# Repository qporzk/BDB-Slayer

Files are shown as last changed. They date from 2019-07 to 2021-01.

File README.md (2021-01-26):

# BDB-Slayer

## NOTE

IF YOU ARE GOING TO PRINT THE STUFF FOR THE JAKE VALVE, SEE NOTE AT BOTTOM OF THIS PAGE

I'm trying out some doc hosting stuff on this repo for fun and to make it look a bit nicer. The readthedocs page is here: https://qporzk.github.io/BDB-Slayer/

This repo is meant to be a knowledge base for mods to the Breville Dual Boiler espresso machine. This focuses on (but is not limited to) the rerouting of tubes to the hot water needle valve to enable flow profiling. Background here: https://www.home-barista.com/espresso-machines/breville-dual-boiler-slayer-shots-t54849.html

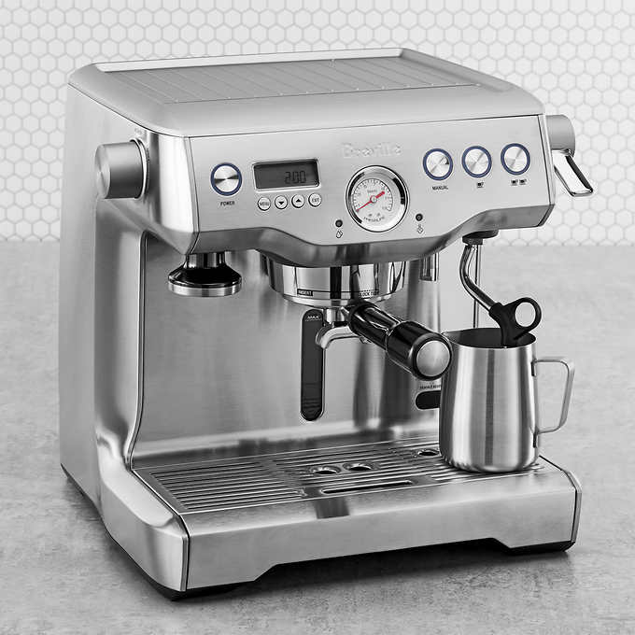
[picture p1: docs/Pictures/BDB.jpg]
Sample Image


## Sections

Slayer Mod
  - This is a pictorial guide to doing this mod

Pulling with the Slayer Mod
  - This focuses on actually pulling shots once the mod is completed. This includes how the pulls work, what the best profiles are, and theory on profiles.

Upgrades
  - This focuses on other upgrades that can be made, including replacing the needle valve, replacing the pump, plumbing in, and others.

Maintenance
  - This covers maintenance, both preventative and reactive, as well as general routine maintenace and cleanup that should be performed

## Models

NOTE: These models are out of date, as they were made for my BDB which was slightly broken. The portion of the body where the hot water knob attaches has a flange that I was unaware of as it was broken off on my machine. I've added an updated .f3d file called "BDB Marker Knob Stock" which may work for new machines, but may need the recess in the knob and cutting of fins on the Drive to be increased in size/depth, as I've only estimated the size of the flange from pictures. If you edit this to fit well on a stock machine, let me know and I can update the model.

This will summarize the 3D models included in the repo, as far as what they are, what they replace, and best practices for acquiring them.

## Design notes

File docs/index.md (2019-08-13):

# BDB-Slayer

## NOTE

I'm trying out some doc hosting stuff on this repo for fun and to make it look a bit nicer. The readthedocs page is here: [GitHub Pages Site](https://qporzk.github.io/BDB-Slayer/)

This repo is meant to be a knowledge base for mods to the Breville Dual Boiler espresso machine. This focuses on (but is not limited to) the rerouting of tubes to the hot water needle valve to enable flow profiling. Background here: [Home Barista Thread](https://www.home-barista.com/espresso-machines/breville-dual-boiler-slayer-shots-t54849.html)

Sample Image

## Sections

Slayer Mod
  - This is a pictorial guide to doing this mod
  
Pulling with the Slayer Mod
  - This focuses on actually pulling shots once the mod is completed. This includes how the pulls work, what the best profiles are, and theory on profiles.
  
Upgrades
  - This focuses on other upgrades that can be made, including replacing the needle valve, replacing the pump, plumbing in, and others.
  
Maintenance
  - This covers maintenance, both preventative and reactive, as well as general routine maintenace and cleanup that should be performed

## Models

[Models for 3D printing can be found here.](https://github.com/qporzk/BDB-Slayer/tree/master/docs/Models)

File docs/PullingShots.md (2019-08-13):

# Pulling Shots
 This will outline different methods to pull shots once the Slayer Mod has been performed.

## Classic Slayer Shot
This mimics the typical shot that would be pulled on an actual Slayer

### Setup
- Set needle valve to barely open 
- Place cup on scale under grouphead
- Hold single cup button to run pump
- Let pump run for 10 seconds
- Divide weight of water by 10 to get your flowrate in ml/s
- Adjust valve and rerun test until you get 1.4ml/s
- Make a mark on the machine so save this position
- Set preinfusion time to 0 seconds

### The Pull
- Install portafilter
- Set valve to 1.4ml/s mark
- Press manual button to start shot
- Preinfuse for desired time
  - Aim to start pressure ramp around 18s
  - First drops should start around 20s 
  - Pressure should get to 9 bar at about 25s
- Open valve for desired amount of full flow time
  - Aim for 2/3 of your total output weight
- Set valve back to 1.4ml/s mark
- Press manual button to stop the shot when target weight is reached (or a bit before)

## Blooming Espresso Shot
This shot mimics the blooming espresso outlined in Scott Rao's blog post: https://www.scottrao.com/blog/2018/7/18/advanced-mode-on-the-de1

### Setup
- Perform pump kill switch mod
- Find and mark 4ml/s point as above
- Find and mark 2.2ml/s point as above
- Set preinfusion time to 0 seconds

### The Pull
- Install portafilter
- Set valve to 4ml/s mark
- Press manual button to start shot
- Preinfuse until pressure ramps to 4bar
- Use kill switch to turn off the pump
- Wait for 30 seconds
- Set valve to 2.2ml/s
- Turn pump back on
- Run shot to desired output weight

## Normal shot
This is just a normal shot ¯\\\_(ツ)_/¯\

### Setup
- Set preinfusion time to desired amount

### The Pull
- Install portafilter
- Set valve wide open
- Press manual button to start shot
- Run shot to desired output weight

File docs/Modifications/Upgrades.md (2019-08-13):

This focuses on other upgrades that can be made, including replacing the needle valve, replacing the pump, plumbing in, and others.

## [Wooden PF Handles](https://www.wilcoxcoffeeparts.com.au/product-category/breville/breville-portafilter-handles/)

## [Brass OPV and Pump Upgrade](https://www.home-barista.com/repairs/breville-dual-boiler-bes900xl-brass-opv-and-pump-mod-t43690.html)

[Alternative Upgrade Site](http://nic.steve-tek.com/?page_id=364)

- [OPV](https://www.espressocare.com/products/item/vibiemme-bypass-valve-opv)
- [Elbow](https://www.ebay.com/itm/1-8-Bsp-Pour-4mm-Compression-Coude-Fixation-Air-Liquide-Qty2-b231-/112089724410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)
- [Pump](https://www.amazon.com/dp/B00B8KBVZE/ref=cm_sw_r_cp_apa_i_7.XmDb7FMQCEF)

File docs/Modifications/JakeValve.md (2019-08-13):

# Summary

This doc covers the "Jake Valve", a replacement for the Hot Water Needle Valve discovered/designed by Jake_G from Home-Barista.

## BOM

- [Clippard Valve](https://www.clippard.com/part/M-MNV-1K)
- [Male push connects](https://www.amazon.com/gp/product/B01N6JF205/ref=ppx_yo_dt_b_asin_image_o00_s00?ie=UTF8&psc=1)
- [Female push connects](https://www.amazon.com/gp/product/B01N6JF205/ref=ppx_yo_dt_b_asin_image_o00_s00?ie=UTF8&psc=1)
- 3D printed shaft and housing

## Procedure

- Remove top cover
- Remove hot water knob by popping off cover and unscrewing screw in center of knob
- Remove two screws holding valve to frame
- Remove two screw holding valve mount inside
- Disconnect two tubes from valve and remove old valve
- Screw female push connect into new valve
- Slide 3D printed shaft onto new valve shaft
- Slide new valve into 3D printed housing, 3D printed shaft first
- Screw male push connect into new valve through hole in housing
- Slide internal mounting bracket onto new assembly
- Reattach tubes
- Reassemble

## Cross section of new assembly

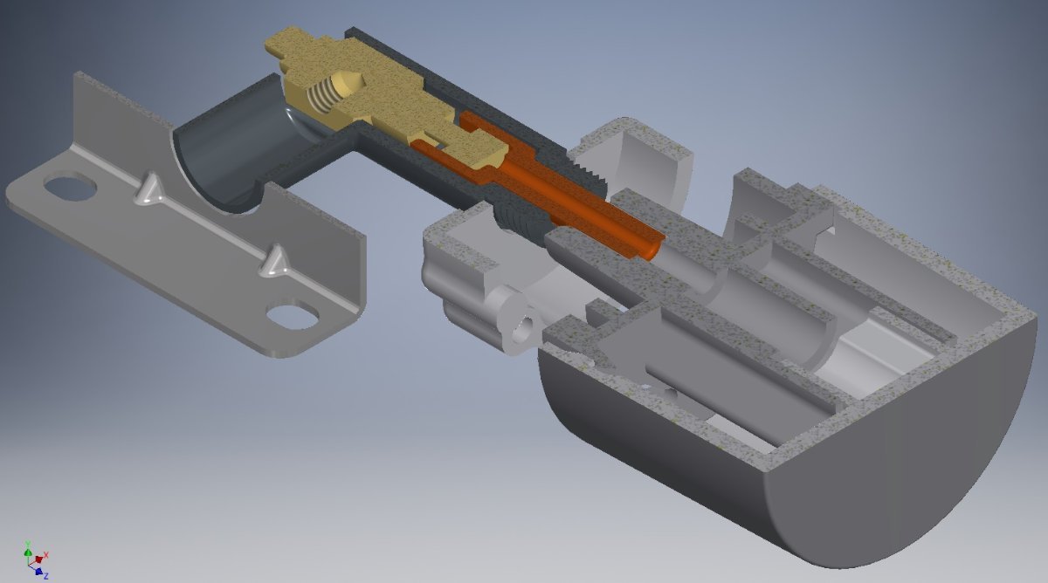
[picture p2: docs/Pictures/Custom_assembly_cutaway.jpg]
Cross Section


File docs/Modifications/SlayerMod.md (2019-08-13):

# BDB Slayer Mod

This outlines the steps needed to perform the Slayer mod on a stock machine as written by user Spitz.me on the Home-Barista forum: https://www.home-barista.com/member/Spitz.me/

## STOCK tube setup on a BDB 920

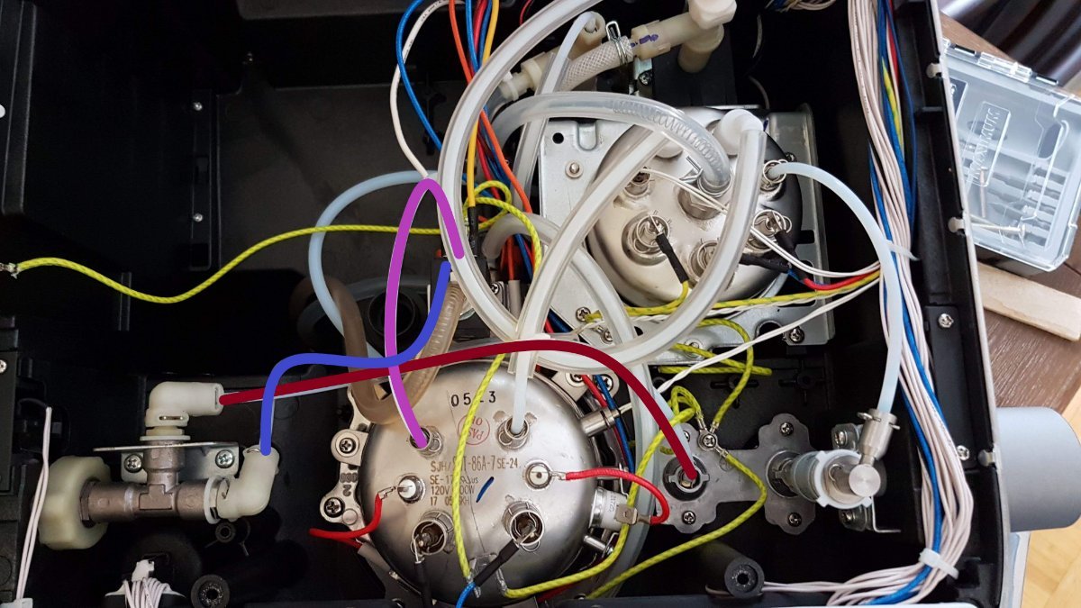
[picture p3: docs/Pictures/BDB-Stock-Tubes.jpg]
Stock BDB tube setup


This is an image taken from the front of the machine so the bottom of the image is the front of the machine.

I'll list the tubes in the order that I did my modification. Also think of the needle valve as a "T". The portion of the needle valve that points to the back of the machine is the middle of the "T". One side of the "T" is the hot water knob.

The tubes have fittings near the ends. These need to go below the hairpin to install the tubes properly. The hairpins can be easily pulled with pliers and they reinstall very easily. This will make more sense when you start working with the tubes.

The tubes may or may not come out with little orange gaskets. You're going to be moving different ends around and even moving an entire tube to a new location. The best thing to do is to take the gaskets with the tubes. If you can't, like I couldn't for one of them, then just be smart about it and move a gasket to another tube. As Ryan pointed out, if you're not careful about your gaskets you could potentially force them awkwardly into the holes and this isn't good.

**Light Purple Tube - Boiler to the solenoid (black box behind the brew boiler)**

**Maroon (dark red) Tube - Needle valve (middle "T" pointing to back) to the hot water tap.**

**Blue Tube - Needle Valve (side "T" pointing to boiler) to the solenoid.**

My tubes and fittings are not the same across all 900s or 920s, I don't believe, but someone smarter can correct me here. I know Peter's 900 has different stock tube fittings. On my machine, all of the tubes I needed to shift had the same hairpin fittings on both ends. I believe my tube hairpin fittings made it easier because removing the tubes from the solenoid would have made it trickier . You can kind of make it out in the picture that the tubes into the solenoid are buried a bit.

## Modified BDB with color coded tubes now in new positions
Detach both tubes from the needle valve. It makes it easier to work through.

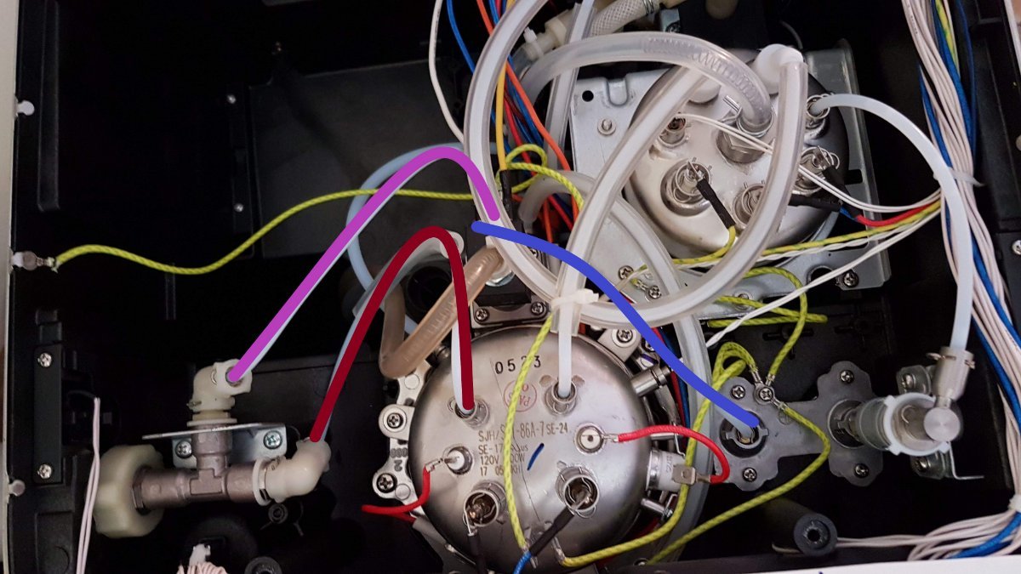
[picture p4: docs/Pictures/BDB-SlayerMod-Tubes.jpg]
Slayer Mod BDB tube setup


### New Configuration:
**Light Purple Tube - Removed from the top of the brew boiler and fitted to the needle valve (middle "T").**

**Maroon (dark red) Tube - Brew boiler to the needle valve (Side "T"). You can see that I simply disconnected this tube from its original setup and re-purposed it. This is the only tube that I fully removed to put somewhere else.**

**Blue Tube - Solenoid to the hot water tap. This tube is really tricky to move into that position because you have to snake it underneath to the other side. I used a coat hanger to raise the tube up so I could grab it once I found my way to a spot just right of the brew boiler. It's TRICKY.**

### Conclusion:
Remove Hot Water Tap switch
Make sure to do the hot water tap mod 
This is where you remove the switch that stops the brew cycle if you turn on the hot water tap. I forgot about this and had to go back in! It's a very easy mod. You can see in my pictures on the left of the valve that mine is still attached (the profiling mod doesn't work if it stays in). It can hang freely after removal.

### Hot Water Tap Plug
Do not forget to plug the hot water tap!!
You can easily unscrew the hot water tap. I didn't outline how to do this as it's been outlined in previous step-by-step posts and detailed a bit more by Peter. Like Ryan, I had no use for the BDB blind plug. So, I followed his method to simply cut out the middle circle of the plug. It fits really nicely as a plug for the hot water tap and I haven't had any leakage whatsoever since I modified the machine 3 weeks ago.

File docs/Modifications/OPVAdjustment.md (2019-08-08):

This is the current best tut on this: http://nic.steve-tek.com/?page_id=180

## Procedure
- Turn off and unplug machine
- Remove the top cover
- Slide hose clamp on OPV back along the hose
  - Squeeze the clamp fully with pliers to make it easy to slide
- Pull the hose off of the OPV
- Remove the locking collar by gently prying up each wing and sliding it off
- Rotate the plastic shaft to adjust the pressure
  - Counter-Clockwise decreases pressure
  - Clockwise increases pressure
  - One quarter turn is approximately equal to 1 bar of adjustment
- Replace the locking collar
- Slide the tube back on
- Slide the clamp back on 
- Turn on machine and test pressure
  - Install portafilter with blind basket
  - Hold 1 cup button
  - Check pressure

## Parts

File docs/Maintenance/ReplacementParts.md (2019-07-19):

## Jake Valve
https://www.clippard.com/part/M-MNV-1K
https://www.amazon.com/gp/product/B01A63RLLQ/ref=ppx_yo_dt_b_asin_title_o02_s00?ie=UTF8&psc=1

## Jake Valve Fittings
https://www.amazon.com/gp/product/B01N6JF205/ref=ppx_yo_dt_b_asin_image_o00_s00?ie=UTF8&psc=1
https://www.amazon.com/gp/product/B07MR1JT34/ref=ppx_yo_dt_b_asin_title_o00_s00?ie=UTF8&psc=1

## Various Parts
https://www.ereplacementparts.com/breville-bes920xl-the-dual-boiler-parts-c-116052_116055_290180.html

## Breville Official
https://www.breville.com/us/en/products/espresso/parts-accessories.BES920.html

## Steam Boiler O-Rings
https://www.amazon.com/gp/product/B0188NN02U/ref=ppx_yo_dt_b_asin_title_o03_s00?ie=UTF8&psc=1

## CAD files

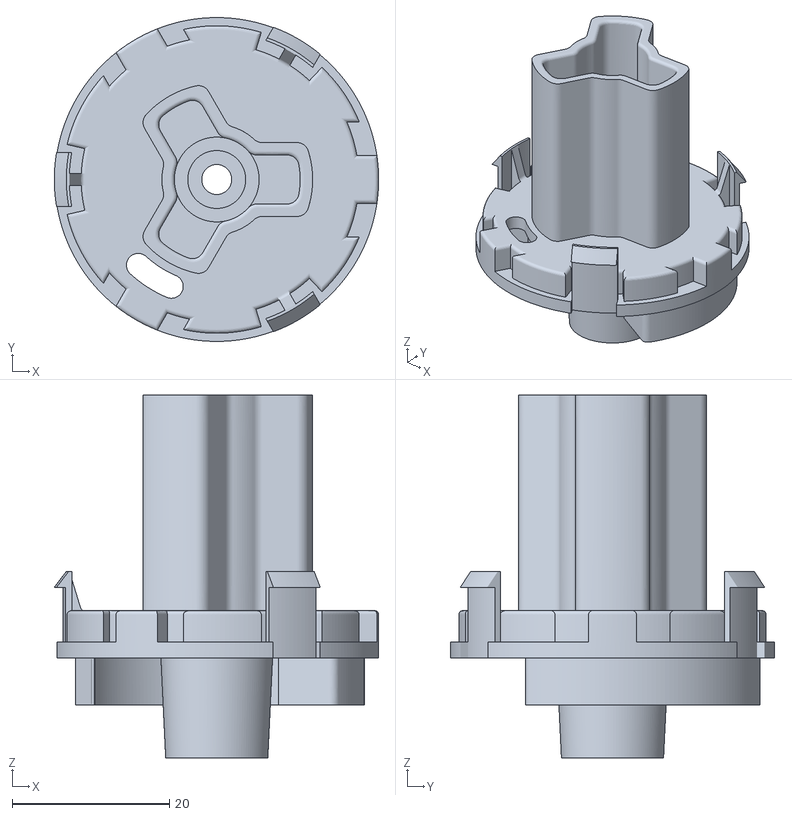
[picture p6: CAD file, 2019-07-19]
site/Models/STL/Stock Assembly_Insert_1.stl
41.3 x 41.2 x 46.2

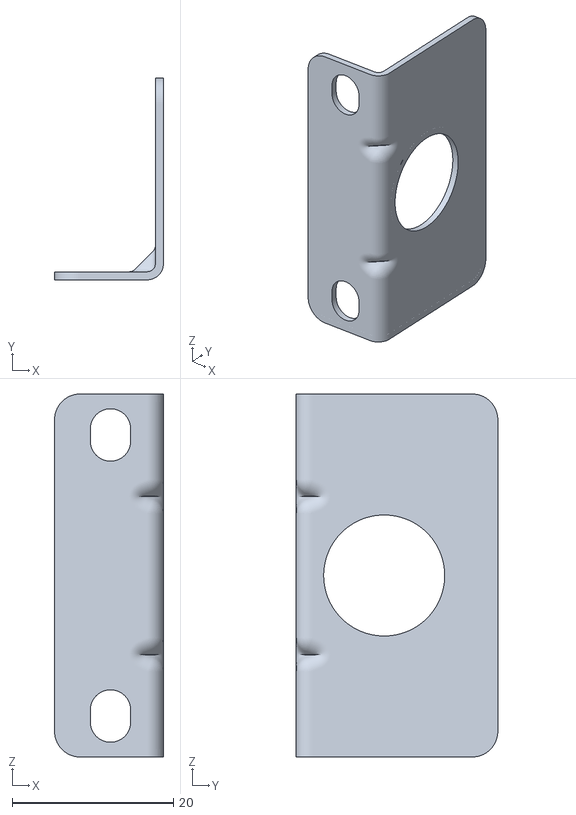
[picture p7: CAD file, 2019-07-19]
site/Models/STL/Stock Assembly_H-Bracket_4.stl
13.5 x 25.0 x 45.0

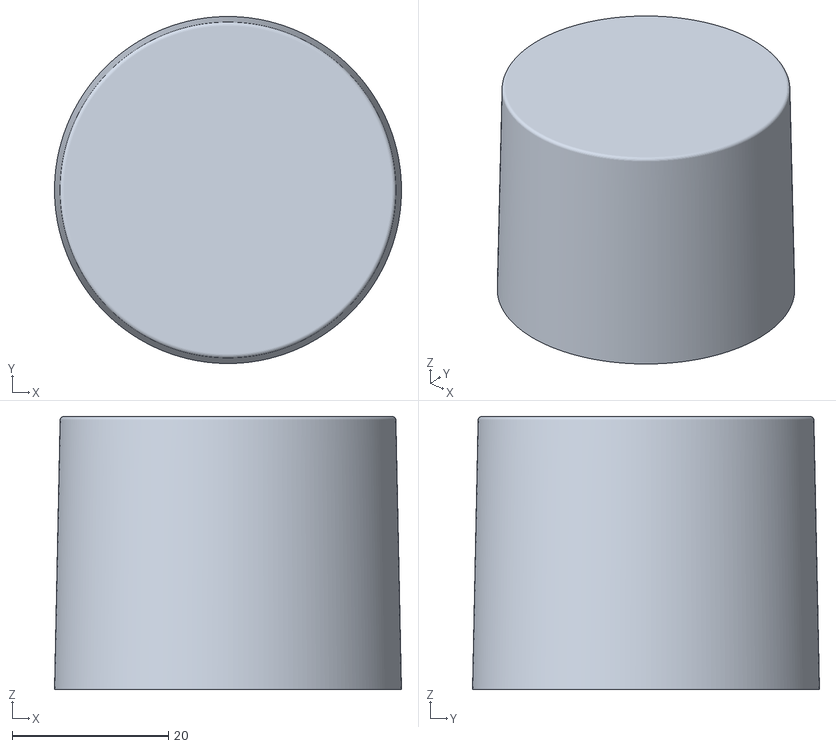
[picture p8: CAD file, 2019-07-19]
site/Models/STL/Stock Assembly_Knob_2.stl
44.5 x 44.5 x 35.0

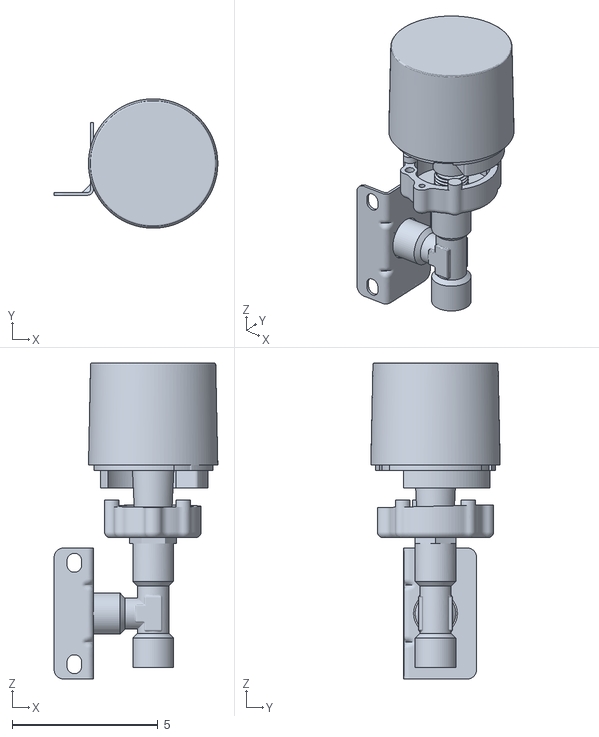
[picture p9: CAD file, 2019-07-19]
site/Models/STL/Stock Assembly.stl
5.62 x 4.44 x 10.9

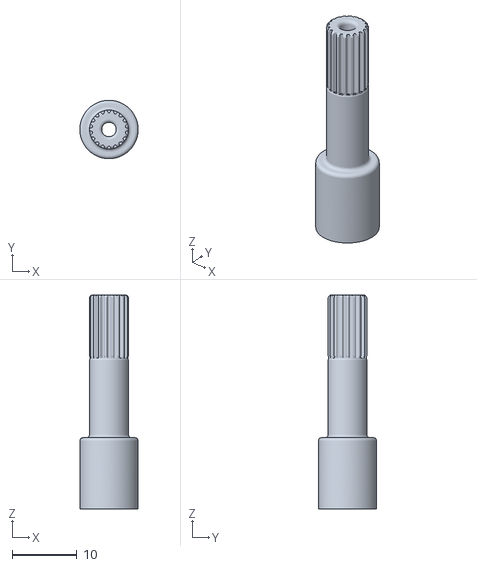
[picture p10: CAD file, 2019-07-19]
site/Models/STL/Stock Assembly_Adapter Shaft_7.stl
9.00 x 9.00 x 33.0

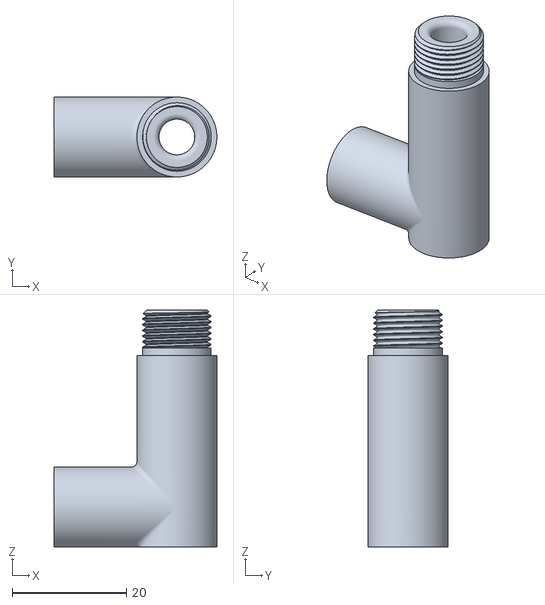
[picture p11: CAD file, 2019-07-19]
site/Models/STL/Stock Assembly_Adapter Body_6.stl
28.5 x 14.0 x 41.5

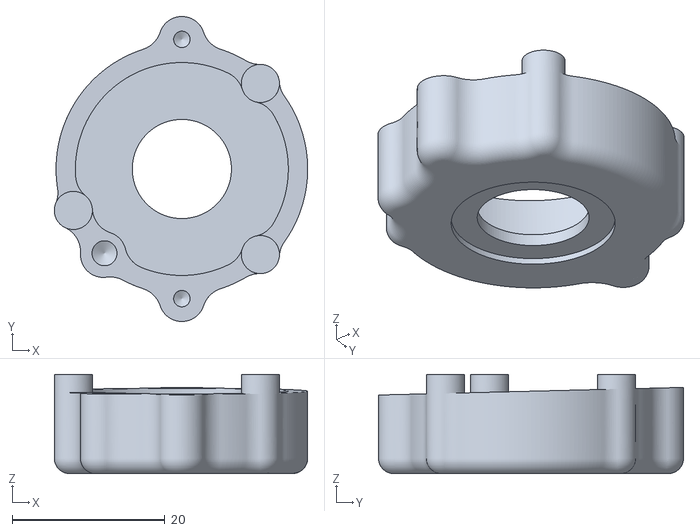
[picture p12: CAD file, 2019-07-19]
site/Models/STL/Stock Assembly_V-Bracket_3.stl
33.2 x 40.0 x 13.0

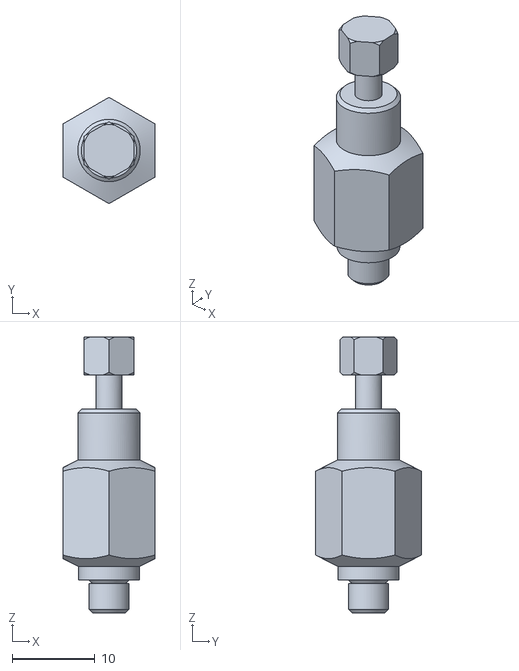
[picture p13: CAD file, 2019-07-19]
site/Models/STL/Stock Assembly_mnv-1k_5.stl
11.1 x 12.8 x 33.3

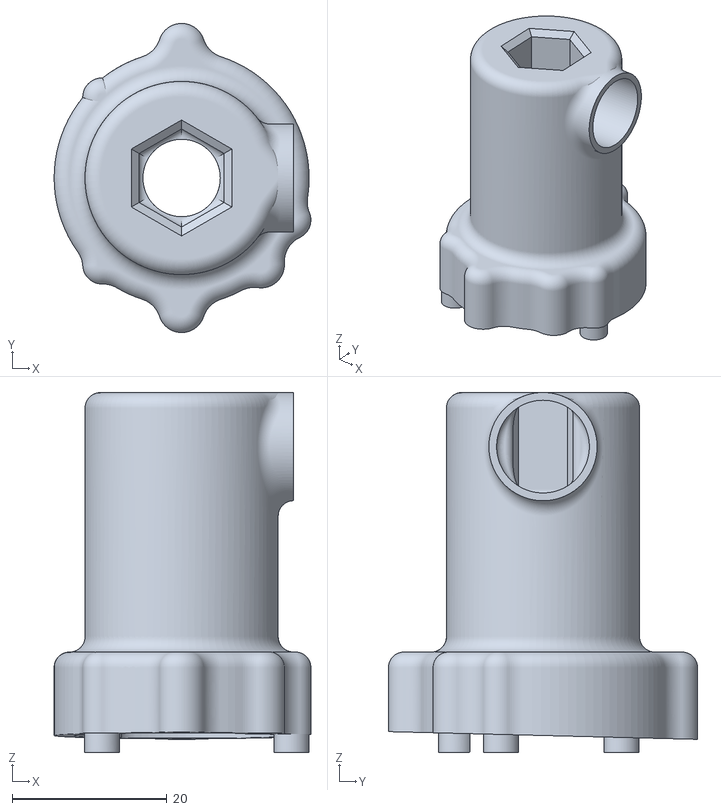
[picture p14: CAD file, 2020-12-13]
docs/Models/STL/Valve Mount_Final.stl
33.2 x 40.0 x 46.6

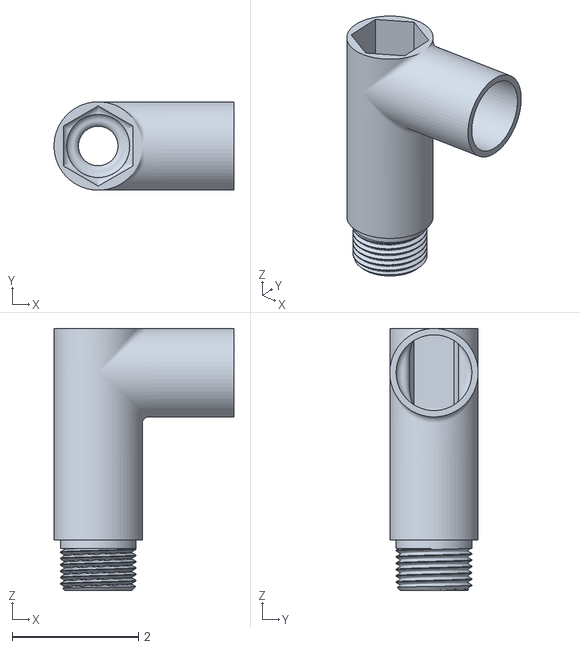
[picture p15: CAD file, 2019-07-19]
site/Models/STL/Adapter Body.stl
2.85 x 1.40 x 4.15

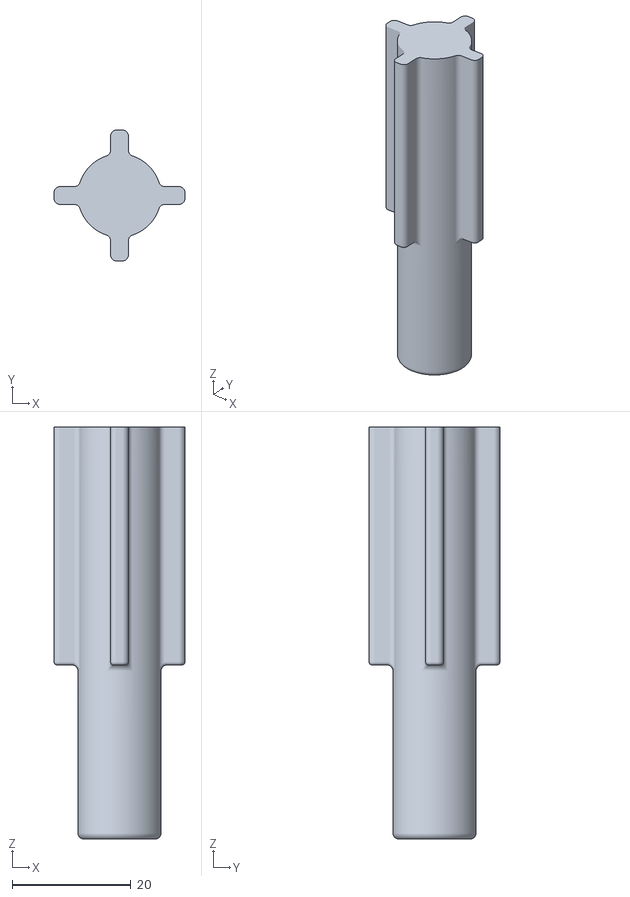
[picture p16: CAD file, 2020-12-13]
docs/Models/STL/Drive_Final.stl
22.0 x 22.0 x 69.2

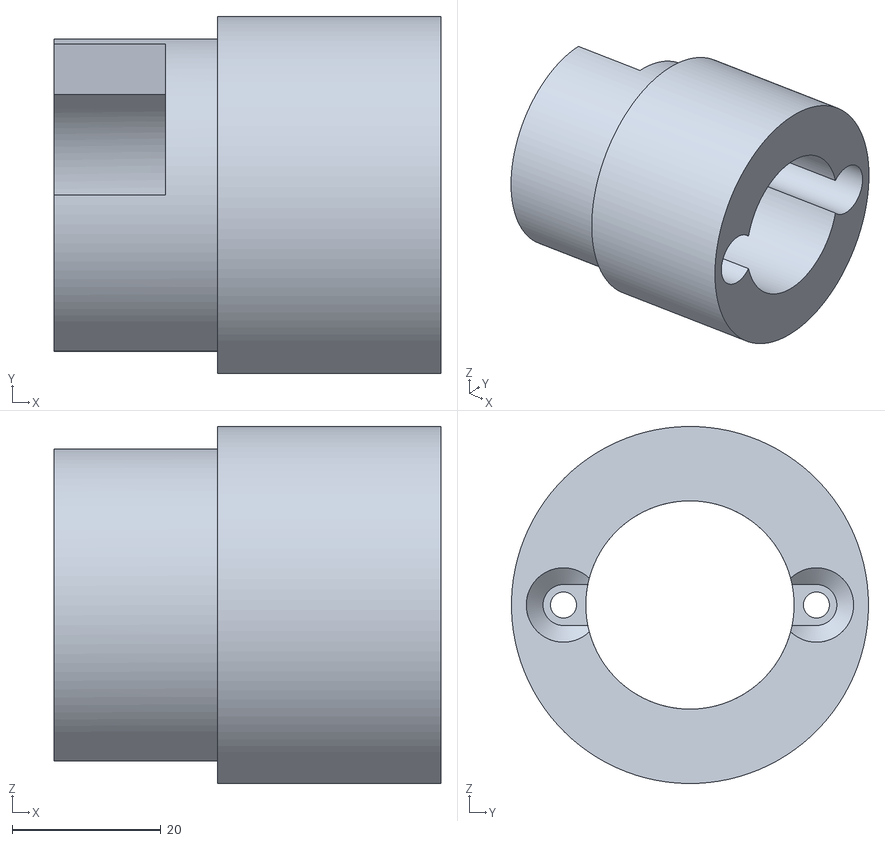
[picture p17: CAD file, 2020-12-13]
docs/Models/STL/Insert_Final.stl
52.0 x 48.0 x 48.0

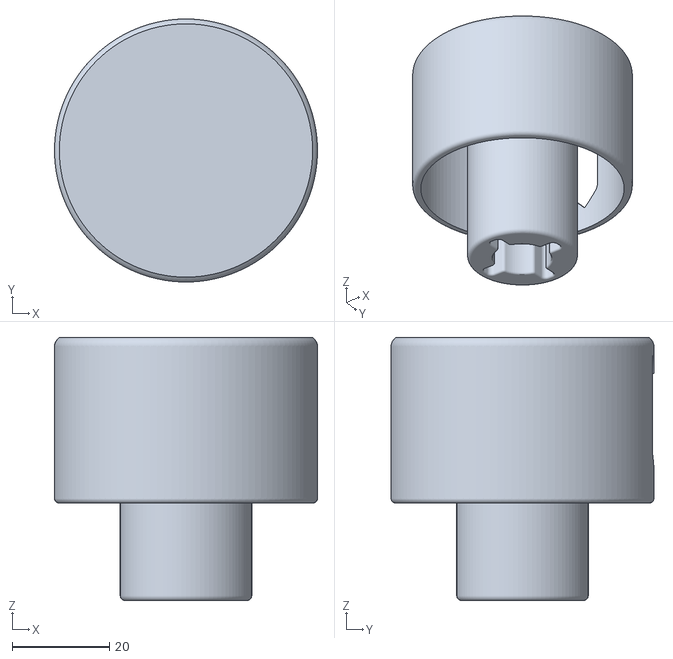
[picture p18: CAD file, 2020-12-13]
docs/Models/STL/Handle_Final.stl
54.0 x 54.0 x 54.0

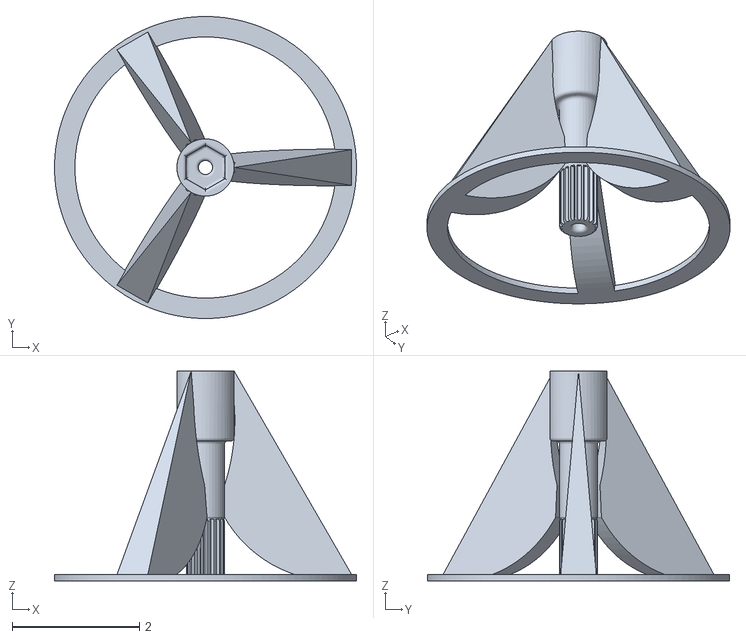
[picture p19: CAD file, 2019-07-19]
site/Models/STL/Adapter Shaft.stl
4.75 x 4.75 x 3.30

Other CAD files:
site/Models/STL/Water_knob.stl
site/Models/CAD/Adapter Body.ipt
site/Models/CAD/Insert.ipt
site/Models/CAD/Knob.ipt
site/Models/CAD/Stock Valve.ipt

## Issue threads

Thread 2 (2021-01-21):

Jack Valve Model issues

mike1808, 2021-01-21:
Thank you very much for providing STL models for Jack Valve mode. I noticed that the model is fitting with the latest BDB machines. In newer models (which is not reflected in the model number) Breville/Sage added the collar around the shaft which prevents your models to fit correctly.

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

If you don't mind I'll submit a PR to Jack Valve page with a note and an updated knob model that works.

qporzk, 2021-01-26:
That would be brilliant, thanks! My machine was broken and didn't have this collar/flange, so I was unaware of it... I've updated the readme to reflect this. I'm also a github amateur so apologies that the branches are a little out of control...

fidalgodev, 2023-11-25:
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

Can you please post the model that fits the new version with the collar? @mike1808

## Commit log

2019-07-30 move all files to docs folder
    [Adapter Body.ipt, Adapter Body.stl, Adapter Shaft.stl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]
2019-08-13 new build
    [Adapter Body.ipt, Adapter Body.stl, Adapter Shaft.stl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]
2019-08-13 add site
    [Adapter Body.ipt, Adapter Body.stl, Adapter Shaft.stl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]
